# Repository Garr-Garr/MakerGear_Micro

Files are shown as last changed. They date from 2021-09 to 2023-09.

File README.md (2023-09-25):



# Introducing the MakerGear MICRO! 

### Description:

This 3D printed 3D printer is designed to be a fun, inexpensive, and easy to build open source project for anyone and everyone! With so many of our customers being in education, we set out to create the perfect tool for STEM education that not only encourages students to use their school's 3D printers, but also helps them better understand the mechanics and technology behind them. Not only do we want users to be able to make their own 3D printer, but we want them to be able to make these printers their own! 

Use any filament, any color, and due to its compact design, it can be printed on (nearly) ANY midsize desktop 3D printer! We have also included the STEP files so feel free to improve or modify this design for whatever parts you may already have on hand.

With the help and feedback of the 3D printing community, we hope to further increase this project's accessibility so that kids of any age or adults with little to no experience can enjoy making their own 3D printer. So please take a look around and maybe try the build for yourself, and if you're up to it, get your kids, or grandkids, or nieces & nephews involved. 3D Printing has been and ALWAYS will be a community. Together we can make the world a better place.

## Specs:
3D-Printable  |   Open-Source   |  DIY 3D-Printer  |  Marlin 2.0  |  TMC2209 Slient Stepper Drivers  |  TFT LCD Screen  |  Bowden Extruder  |  MK8 Hotend (rated up to 250°C)  |  89x89x100mm Build Volume  |  12Volt Power Supply

## User Guides:



### Built from MakerGear Kit:

* [Getting Started Guide](https://github.com/MakerGear/MakerGear_Micro/blob/main/Guides/Built_From_Kit/MICRO%20Getting%20Started%20Guide%20(kit).pdf)
* [Mechanical Assembly Guide](https://github.com/MakerGear/MakerGear_Micro/blob/main/Guides/Built_From_Kit/MICRO%20Mechanical%20Assembly%20Guide%20(kit).pdf)
* [Wiring Guide](https://github.com/MakerGear/MakerGear_Micro/blob/main/Guides/Built_From_Kit/MICRO%20Wiring%20Guide%20(kit).pdf)

### Built from scratch:

* [Getting Started Guide](https://github.com/MakerGear/MakerGear_Micro/blob/main/Guides/Built_From_Scratch/MICRO%20Getting%20Started%20Guide%20(scratch).pdf)
* [Mechanical Assembly Guide](https://github.com/MakerGear/MakerGear_Micro/blob/main/Guides/Built_From_Scratch/MICRO%20Mechanical%20Assembly%20Guide%20(scratch).pdf)
* [Wiring Guide](https://github.com/MakerGear/MakerGear_Micro/blob/main/Guides/Built_From_Scratch/MICRO%20Wiring%20Guide%20(scratch).pdf)

## Hardware:

* [Printed Parts](https://github.com/MakerGear/MakerGear_Micro/tree/main/Hardware)

## Printer Slicing Profiles:
* [Simplify3D](https://github.com/MakerGear/MakerGear_Micro/tree/main/Slicer_Profiles/Simplify3D)
* [PrusaSlicer](https://github.com/MakerGear/MakerGear_Micro/tree/main/Slicer_Profiles/PrusaSlicer)

## USB Driver:

While the Micro is fully controllable using the LCD screen and an SD Card/USB stick, you can directly connect the Micro to your computer via USB by downloading the USB drivers from BigTreeTech's page below:

> https://github.com/bigtreetech/BIGTREETECH-SKR-mini-E3/tree/master/firmware/mapleDrv-USBdriver

## Building Marlin 2.0 (Version: [2.0.9.1](https://github.com/MarlinFirmware/Marlin/releases/tag/2.0.9.1))
The firmware is already compiled and ready to upload onto your Micro, but you'd like to make any upgrades or changes to the firmware you'll need to compile the firmware. To compile and upload the firmware you'll need [Arduino IDE 1.8.8 or newer](https://www.arduino.cc/en/main/software) or [PlatformIO](http://docs.platformio.org/en/latest/ide.html#platformio-ide). Detailed build and install instructions are posted at:

  - [Installing Marlin (Arduino)](http://marlinfw.org/docs/basics/install_arduino.html)
  - [Installing Marlin (VSCode)](http://marlinfw.org/docs/basics/install_platformio_vscode.html).

## Inquiries:

Please contact "Print@MakerGear.com" if you have any questions, concerns, or even general feedback on the project!

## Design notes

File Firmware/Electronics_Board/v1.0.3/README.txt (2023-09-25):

Step 1: Format a MicroSD Card to the "FAT32" or "exFAT" filesystem

Step 2: Copy the "Firmware.bin" file onto the SD card

Step 3: Safely eject the SD card from your computer

Step 4: Insert the firmware SD card into the MicroSD card port on the SKR Mini e3 V2 electronics board

Step 5: Reset or reboot the printer (There is a small white reset button close to the MicroSD card adapter on the board)

Step 6: The TFT LCD screen should automatically connect once the firmware is finished uploading

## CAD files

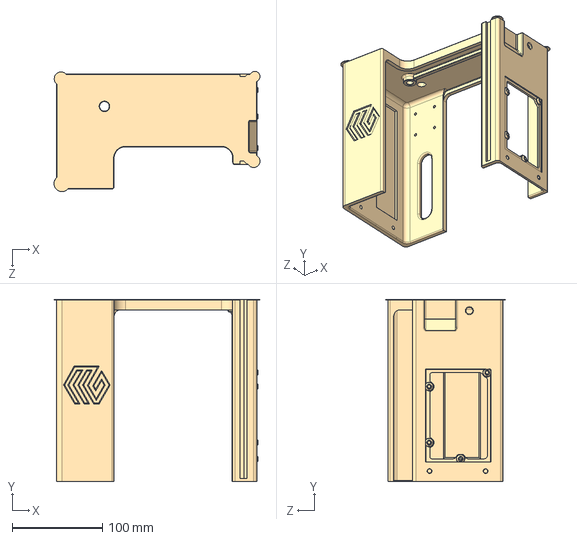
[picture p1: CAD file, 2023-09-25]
Hardware/STEP_Files/MICRO_Top.STEP
228.6 x 202.3 x 133.5 mm

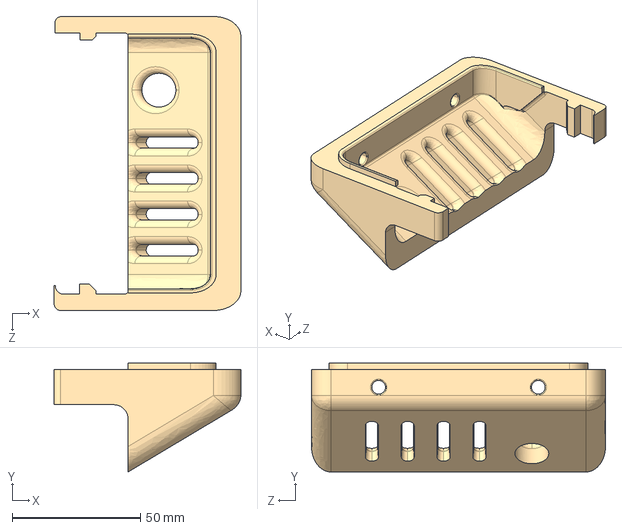
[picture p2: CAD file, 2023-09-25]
Hardware/STEP_Files/MICRO_ElectronicsCaseBase.STEP
72.7 x 42.5 x 114.6 mm

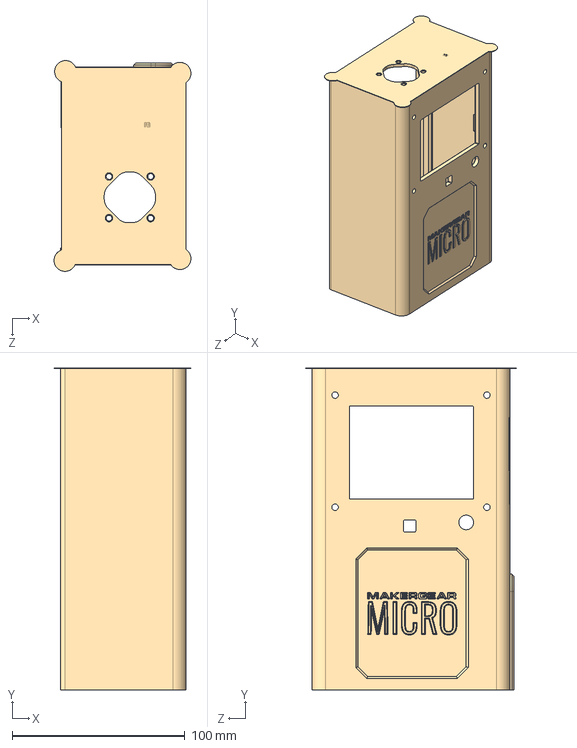
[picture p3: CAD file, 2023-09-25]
Hardware/STEP_Files/MICRO_ElectronicsCase.STEP
79.3 x 186.6 x 122.2 mm

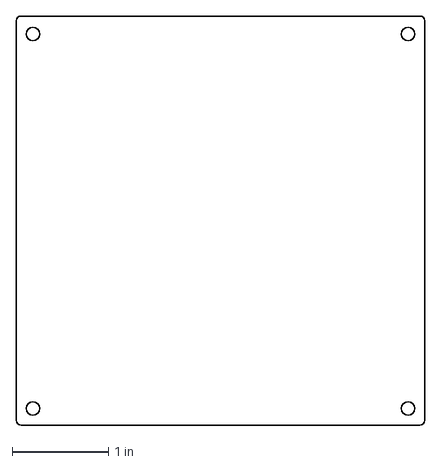
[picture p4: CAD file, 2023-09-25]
Hardware/STEP_Files/MICRO_LaserCutBed.DXF
4.25 x 4.26 in

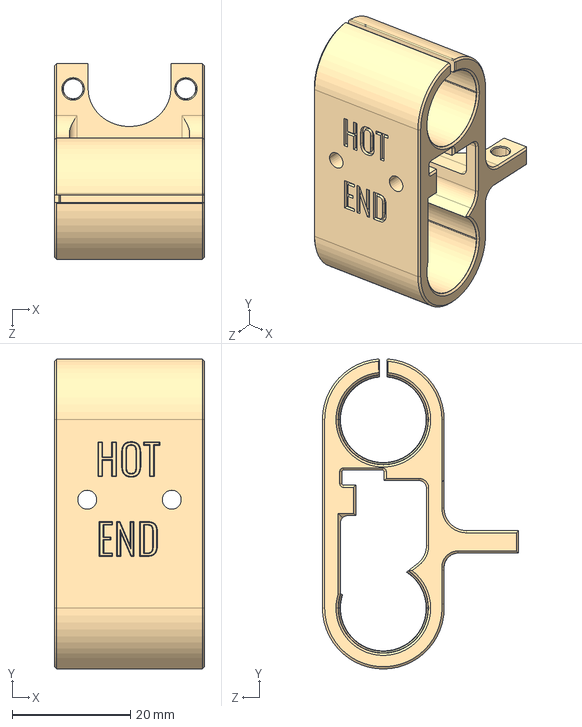
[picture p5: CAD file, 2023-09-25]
Hardware/STEP_Files/MICRO_HotEndMount.STEP
25.4 x 52.4 x 33.2 mm

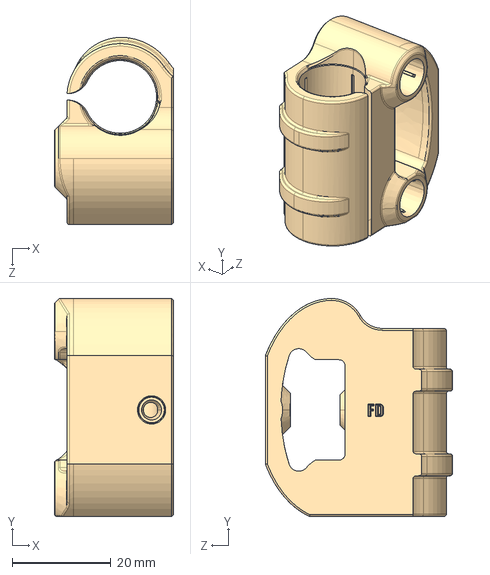
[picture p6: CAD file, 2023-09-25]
Hardware/STEP_Files/MICRO_XIdlerMount.STEP
24.1 x 44.1 x 37.9 mm

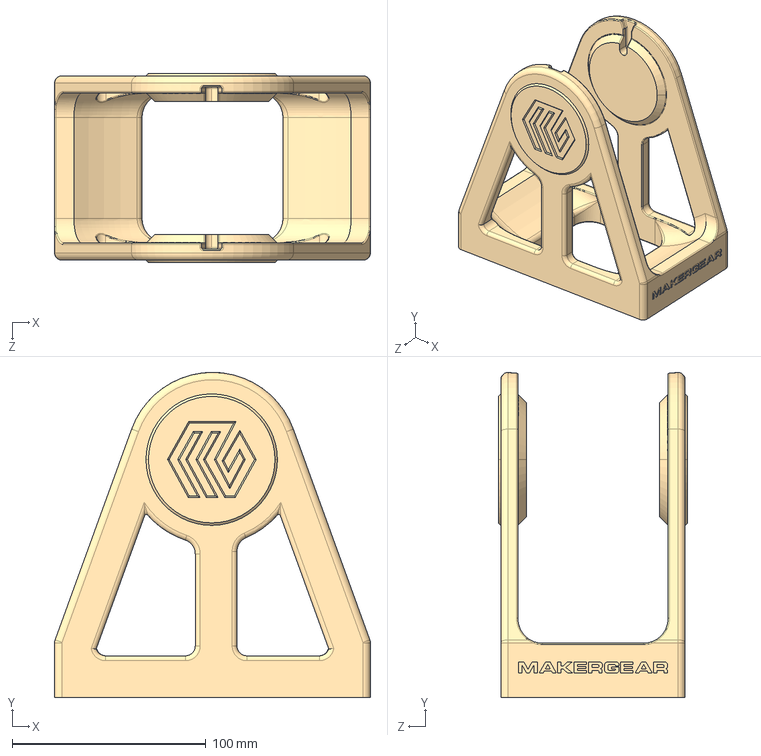
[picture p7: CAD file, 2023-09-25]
Hardware/STEP_Files/MICRO_SpoolHolder.STEP
163.2 x 168.0 x 97.8 mm

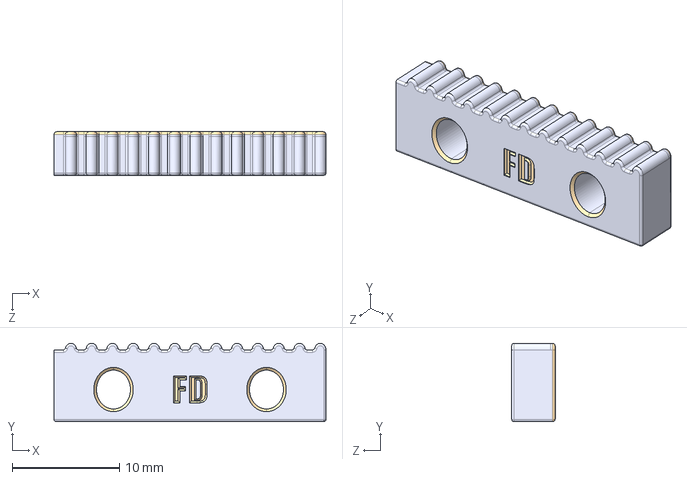
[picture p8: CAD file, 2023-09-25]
Hardware/STEP_Files/MICRO_XBeltGrip.STEP
25.4 x 7.32 x 4.06 mm

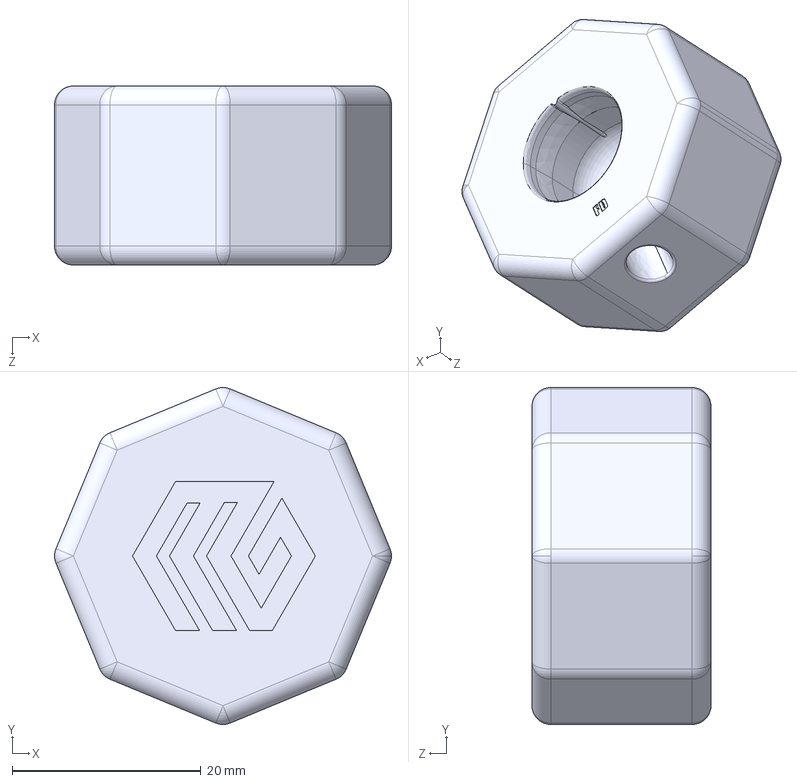
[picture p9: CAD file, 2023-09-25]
Hardware/STEP_Files/MICRO_ZKnob.STEP
35.8 x 35.8 x 19.0 mm

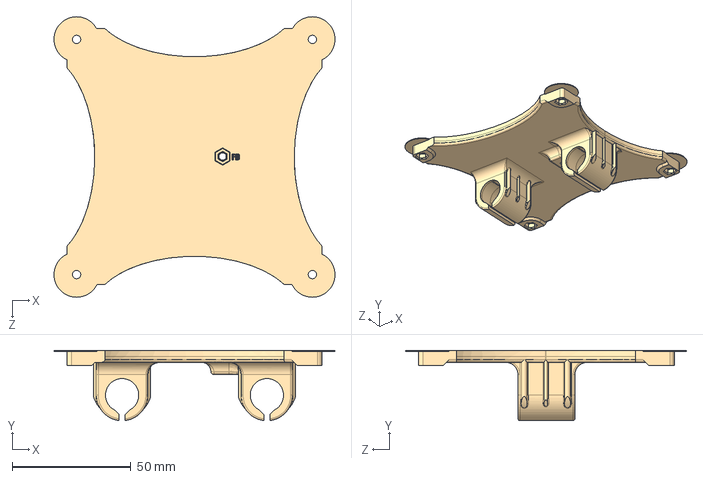
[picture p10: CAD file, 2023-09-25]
Hardware/STEP_Files/MICRO_Bed.STEP
118.3 x 29.6 x 118.1 mm

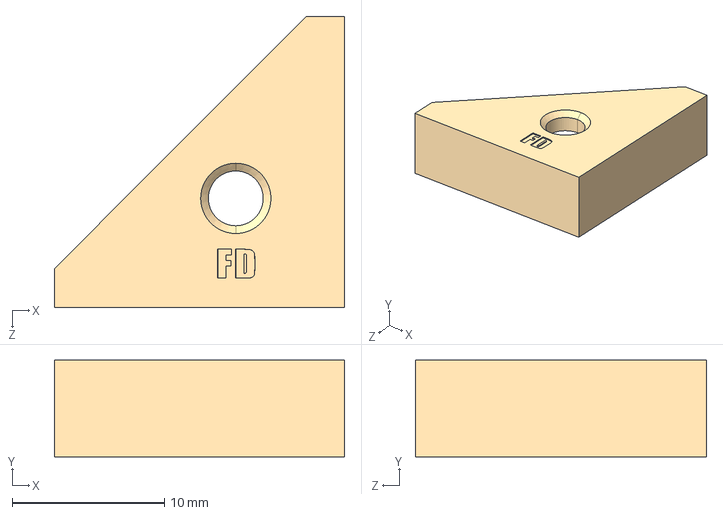
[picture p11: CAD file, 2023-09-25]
Hardware/STEP_Files/MICRO_BedClip.STEP
19.1 x 6.35 x 19.1 mm

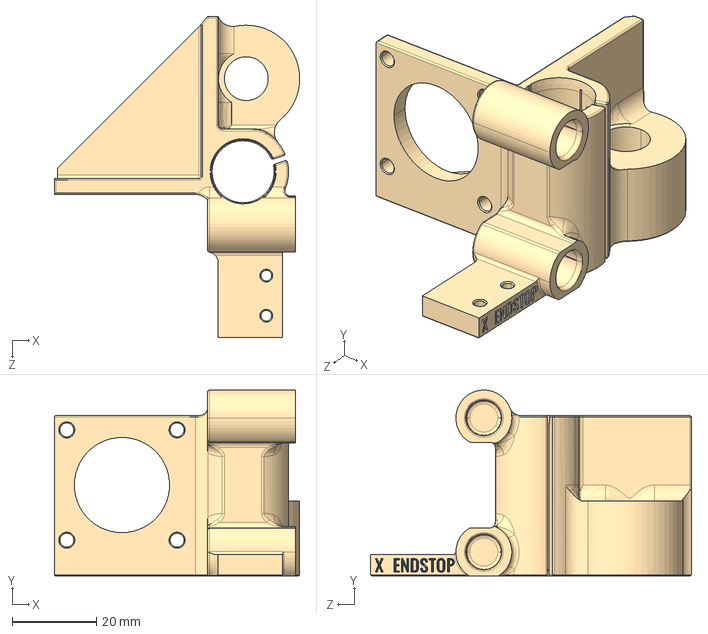
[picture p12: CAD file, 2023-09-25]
Hardware/STEP_Files/MICRO_XMotorMount.STEP
58.3 x 44.2 x 76.2 mm

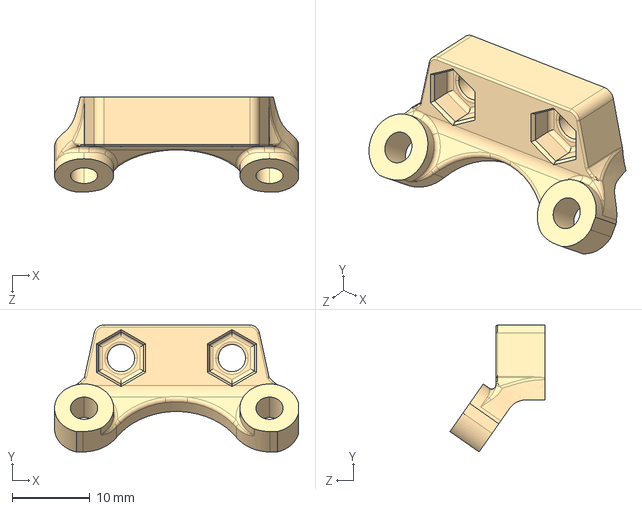
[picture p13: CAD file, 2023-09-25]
Hardware/STEP_Files/MICRO_FanMount.STEP
31.4 x 16.4 x 12.2 mm

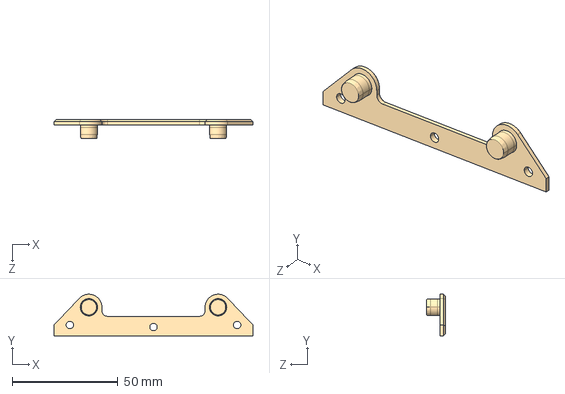
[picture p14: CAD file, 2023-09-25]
Hardware/STEP_Files/MICRO_YStop.STEP
93.9 x 19.6 x 9.02 mm

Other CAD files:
Hardware/STL_Files/MICRO_Bed.stl
Hardware/STL_Files/MICRO_BedClip.stl
Hardware/STL_Files/MICRO_ElectronicsCase.stl
Hardware/STL_Files/MICRO_ElectronicsCaseBase.stl
Hardware/STL_Files/MICRO_FanMount.stl
Hardware/STL_Files/MICRO_HotEndMount.stl
Hardware/STL_Files/MICRO_XIdlerMount.stl
Hardware/STL_Files/MICRO_XMotorMount.stl
Hardware/STL_Files/MICRO_YStop.stl
Hardware/STL_Files/MICRO_ZKnob.stl

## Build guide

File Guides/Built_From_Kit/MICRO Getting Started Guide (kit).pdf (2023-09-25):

# MAKERGEAR

# MICRO

# GETTING STARTED GUIDE

BUILT FROM KIT EDITION

# READ EVERYTHING PLEASE!

If you have chosen to build this thing from scratch, there are SO MANY little tiny things that might go wrong... So, we made one of our hyperactive engineers sit down & spend a COUNTLESS number of HOURS producing LOTS of detailed documentation to help YOU succeed. We’ll be honest there is like a LOT of verbiage in the next 10 pages & it might get boring, but you should read it. All of it. If not for yourself, do it for that poor engineer & the nights he worked late in

the hopes of making YOUR life easier.
Don’t let all that hard work be made in vain.

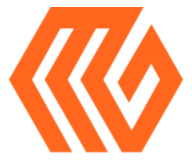
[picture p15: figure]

1

# BEFORE PLUGGING IN

## A Convenient Checklist to Make Sure Nothing Blows Up… Just Kidding

-Check EVERY wire connection! Each connector used in this kit should provide a nice snug connection either popping into place or being latched together. NO connection should be loose or easily removable. If a connection does seem loose, double check that it is plugged into the correct location with the proper orientation.
-Physically slide the machine’s X, Y, & Z axis to confirm a proper mechanical assembly.
-Start with the Y axis by sliding the bed back & forth. Ensure that it travels smoothly without much resistance and can reach the Y End Stop successfully. The Y End Stop should click once the bed reaches it. When sliding the bed make sure the belt properly rotates both the Idler Pulley at the front of the machine, as well as the Drive Pulley mounted onto the Y Motor.
-Now check the X Axis by sliding the Hot End Mount from side to side. Confirm that it slides smoothly without interruption & that it successfully triggers the X End Stop once slid all the way to the left. Give the Hot End assembly a very light wiggle to check that it is securely fastened to the Hot End Mount. Lastly check that the belt is held snug withing the Hot End Mount by giving it a few gently tugs. This belt MUST be secure for your machine to succeed.
-Lastly check the Z Axis by turning the Z Knob both clockwise and counterclockwise. The entire X Axis assembly should move up and down relatively easy. You will feel the motor subtly click repeatedly as you manually rotate the Z Knob, this is normal. Make sure to not dig the tip of the nozzle into the bed when lowering or grind the entire assembly into the roof when raising the axis. -Make sure to raise the Hot End at least an inch above the bed before plugging in your machine. The BL Touch Probe will deploy every time the machine is turned on and needs space to fully deploy or else it will fail its initial start up tests & the machine will need restarted.

2

# NOW PLUG IN!

## We are ALMOST there… Just a Little Housekeeping First

-As mentioned on the last page, once plugged in the BL Touch probe will initiate a short test in which it deploys & retracts twice each. If it does not do this, something could be wrong with the probe or its connection.
-Once the screen turns on, you might be greeted by the prompt below, in which case you’ll select “Touch Mode”

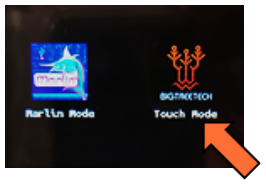
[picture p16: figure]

-Does “Marlin Mode” work with this device? Yes. Is it nearly as cool? NO… but if you insist or if you accidentally hit the wrong mode, pressing the screen’s knob like a button, and holding it for several seconds will allow you to return to this selection screen.
-You should end up at a screen like the one pictured below. You will also be greeted by a “Bed Leveling Failed” prompt. Ignore it. We’ll address that a few steps from now. Make sure to follow along with the orange arrows provided by this guide.

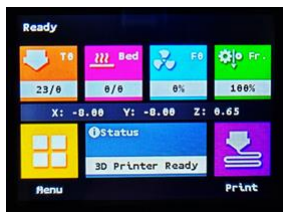
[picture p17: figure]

3

# AFTER PLUGGING IN

## These Next Steps MUST be Completed Before Your MICRO’s First Print

Next, we want to test the 3 axis motors by homing all 3 axis. Both the X and Y axis will move into their respective limit switches, activating them twice before settling into their home position. The Z axis will raise slightly and then lower the probe into the center of the bed twice. If all 3 axis home as described, proceed to the next step. If not, there could be an issue with your motor connections.

## HOW TO HOME YOUR MACHINE

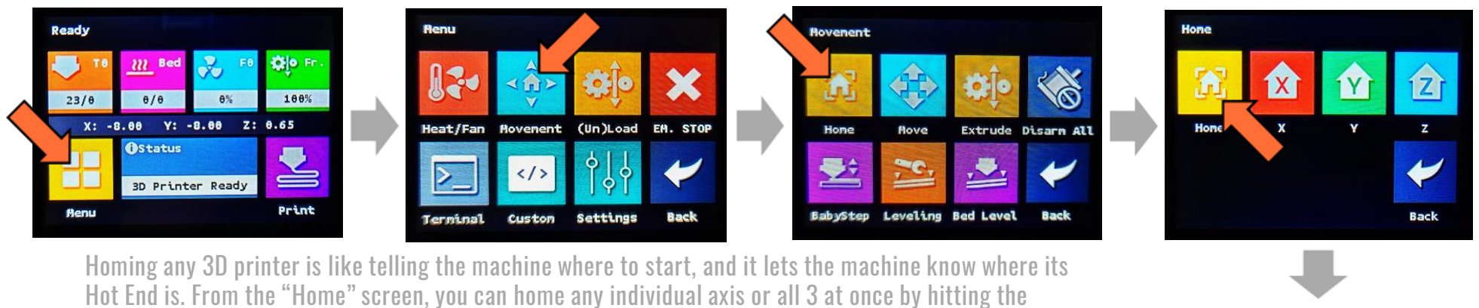
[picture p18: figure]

Homing any 3D printer is like telling the machine where to start, and it lets the machine know where its Hot End is. From the “Home” screen, you can home any individual axis or all 3 at once by hitting the yellow “Home” button. Always make sure the bed is clear & nothing can impede the machine’s movement before homing. Let the homing sequence finish completely before advancing to the next steps.

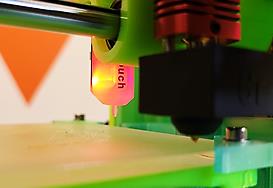
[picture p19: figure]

4

# AFTER PLUGGING IN [cont.]

Once homing is completed, the probe offset must be set. This tells the MICRO how far the tip of the nozzle is from the tip of the BL Touch probe. If set correctly your first layers will be placed the perfect distance above the bed and will properly adhere to the bed surface. If this value is too high, the nozzle will be too far from the bed & none of the printed plastic will stick properly to the bed. If too low, the nozzle will be ground into the bed and the plastic will come out too squished or not at all.

## SETTING THE PROBE OFFSET

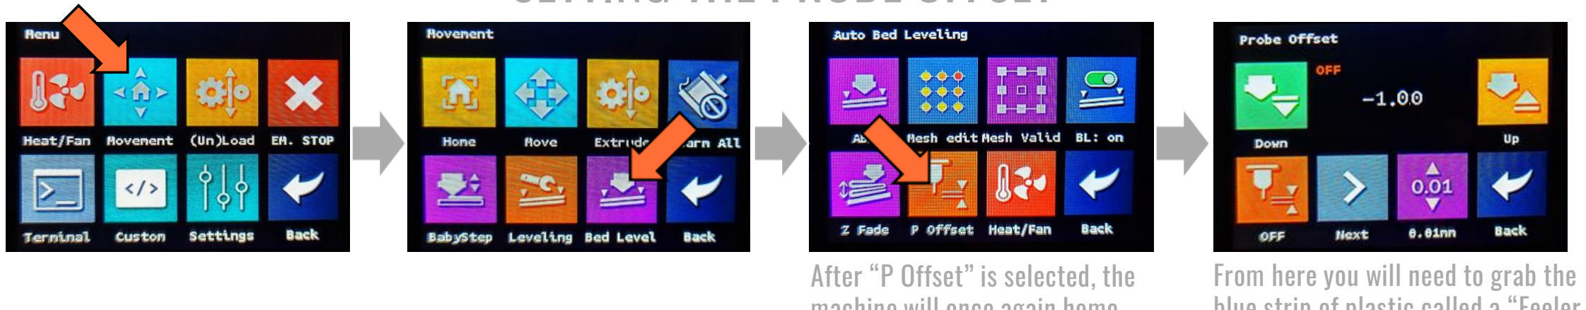
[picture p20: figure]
After “P Offset” is selected, the; From here you will need to grab the

machine will once again home the Z axis.

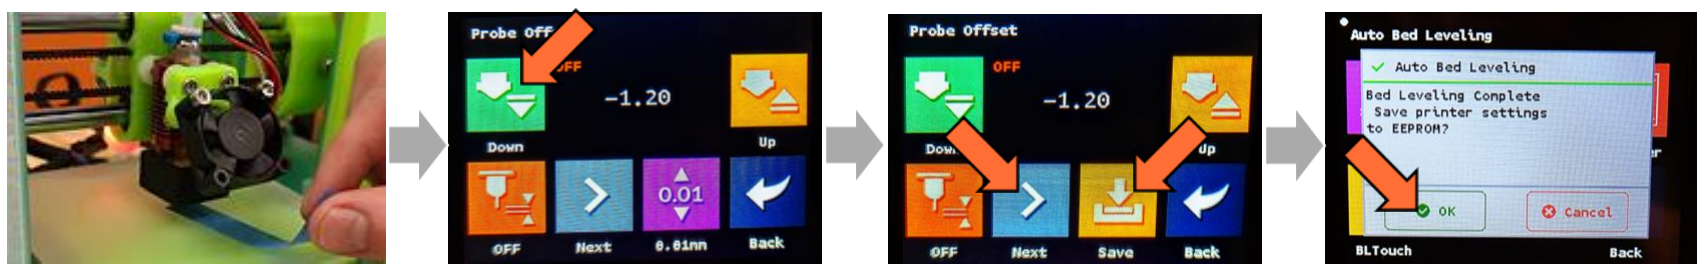
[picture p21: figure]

Place the Feeler Gauge beneath the tip of the nozzle and use the “Down” button to lower the nozzle towards the bed. Lower the nozzle until it just barely touches the Feeler Gauge. The increments in which the nozzle moves can be tweaked via the purple button initially labeled, “0.01mm”

Once you feel that the perfect offset value has been reached, hit the “Next” button twice or until the “Save” button appears next to hit. Select “Save” and the following prompt will pop up to which you respond, “OK” blue strip of plastic called a “Feeler Gauge” from the provided tool kit.

5

This setting is essentially the equivalent of Automatic Bed Leveling which will make sure that your first layers are always flat & flush with your bed. If not set properly, the nozzle will vary in its distance from the bed while printing. This can cause portions of the print to not stick properly or not extrude at all which will almost always cause your print to fail

## ACTIVATING BED LEVEL COMPENSATION

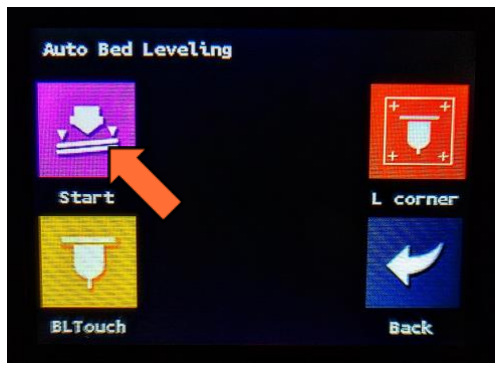
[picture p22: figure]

Pressing “Start” will lead into the machine’s probing sequence during which the printer will generate a mesh. This mesh basically let’s the printer know how the bed is shaped/slanted & will use the Z Motor to compensate for these variations while printing.

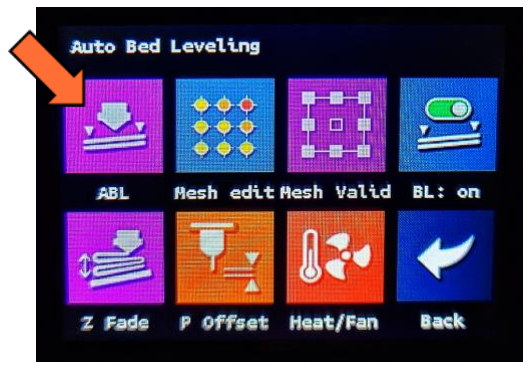
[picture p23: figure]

Return once more to the “Auto Bed Leveling” screen (found under the “Movement” option in the main menu)

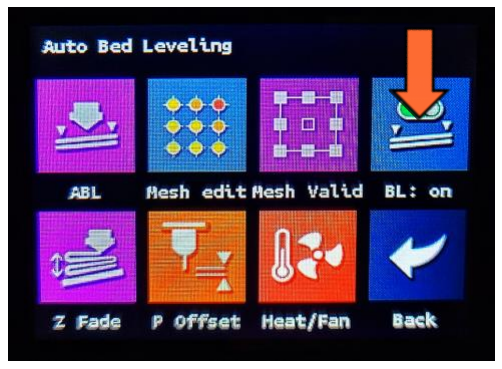
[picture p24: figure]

Before returning to the main menu, make sure the BL Touch is activated by hitting this button. It should display “BL: on” and can be toggled on & off with each press.

# AFTER PLUGGING IN [cont.]

6

Finally, we will be loading filament into your MICRO. Only use a PLA that has a recommended printing temperature range that includes 190°C or below. You may need to straighten out the first couple inches of the filament’s end to help thread it into the filament drive.

## LOADING THE FILAMENT

# AFTER PLUGGING IN [cont.]

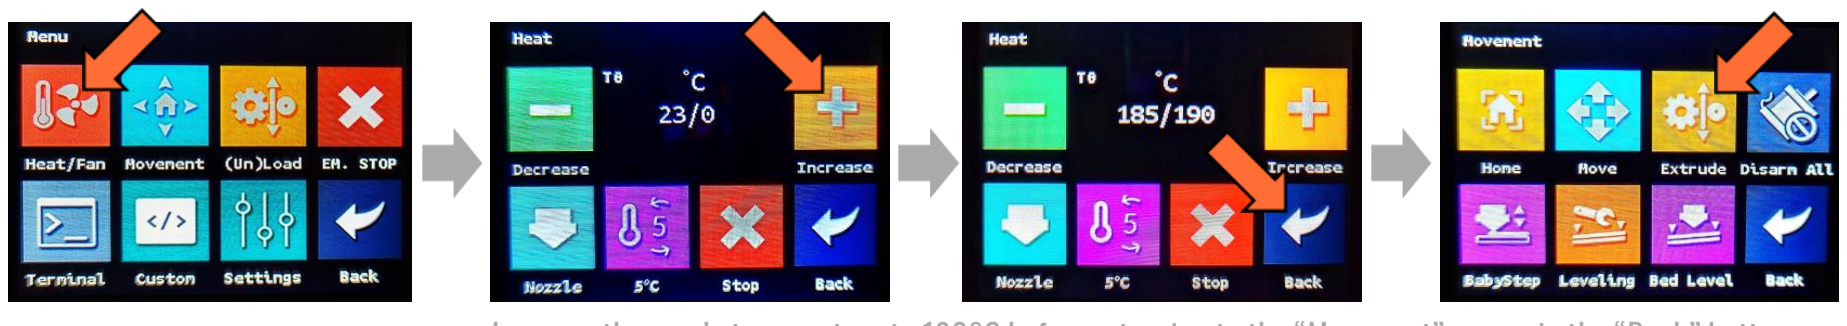
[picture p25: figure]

Increase the nozzle temperature to 190°C before returning to the “Movement” menu via the “Back” button. The left temperature value in white is the actual temp, while the right value is the temp you set it to.
You can adjust your temperature increments via the purple button initially labeled “5°C”

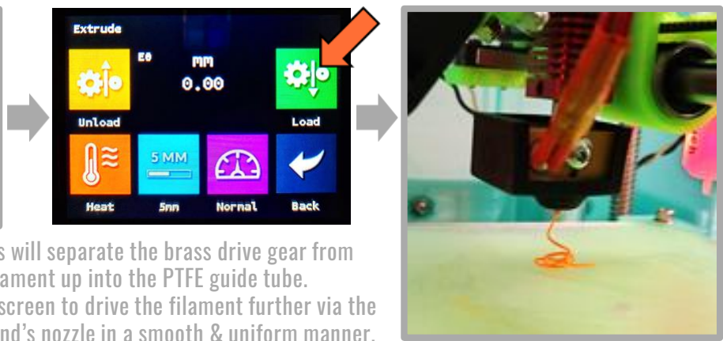
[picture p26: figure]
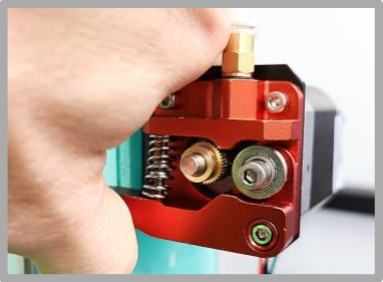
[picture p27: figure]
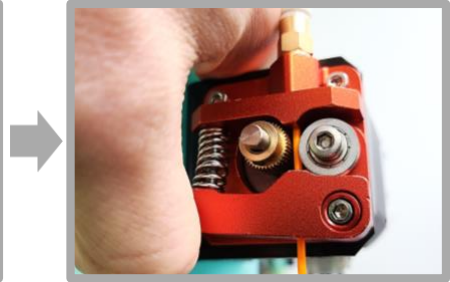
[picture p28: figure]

Pinch the lever of the MICRO’s filament drive to compress the spring. This will separate the brass drive gear from the silver bearing/pulley creating a space for you to feed an end of the filament up into the PTFE guide tube. Manually feed the filament until it reaches the hot end, and then use the screen to drive the filament further via the “Load” button. Continue to load filament until it extrudes out of the hot end’s nozzle in a smooth & uniform manner.

7

# STARTING YOUR FIRST PRINT

## Wow… Here We Go!

-Make sure one more time that the print bed is clear and free of debris.
-Confirm that your filament is loaded, and that the spool is placed within a spool holder directly next to the filament drive. This spool of filament must be fed directly upwards into the filament drive allowing the filament to unwind in a natural manner. -Plug the included SD Card into the SD slot next to the touch screen. This is where you’ll store gcodes for all of your prints. -Confirm your MICRO is placed on a sturdy surface in a well-ventilated space.
-Start your print…

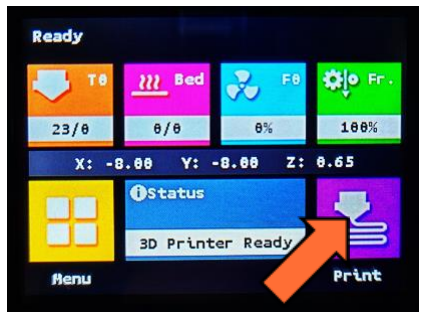
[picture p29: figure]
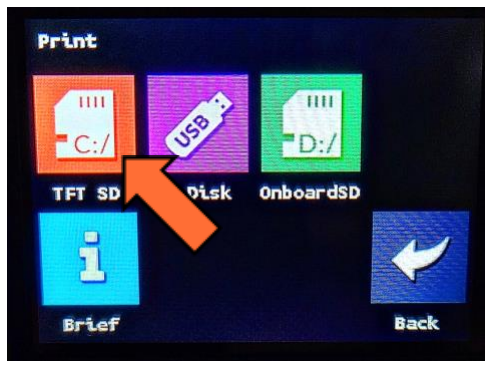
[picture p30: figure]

-Once heated up, the machine will go directly into its first layers. Be prepared to cancel the print if the first layers are not adhering properly. If the nozzle simply seems slightly too close or too far, you can use the Z Knob to make small adjustments, one click at a time.

Select the gcode file you’d like to print. We suggest starting with the “MICROVase” as a test.

8

# PRINTING WITH THE MICRO

## A Random List of Tips & Tricks to Set You up for Success

-ONLY use PLA when printing. You made a 3D printed 3D printer NOT an industrial machine for prototyping with exotic materials.
-We suggest printing on this machine with a layer height of .2mm or higher.
-A print speed of 40mm per second or slower is highly recommended. This will decrease the likelihood of the belts slipping or the smaller X and Y motors from skipping. These problems can be recognized by layer shifts mid print.
-NEVER Exceed a printing temperature of 200°C. Since we are using such a small cooling fan, over time the heat might leak upwards and start melting your printer if the nozzle temp is set too high.
-For the same reason as the previous point, NEVER operate the printer if the Hot End’s cooling fan is malfunctioning. Make sure this fan is running at the start of EVERY print. The fan should come on automatically anytime the nozzle temperature exceeds 30°C
-DO NOT remove the PTFE tubing or Nozzle from the Hot End Assemble unless absolutely necessary. With this style of Hot End, removing/replacing either one of these will highly increase your chances of the assembly clogging or getting jammed.
-NEVER operate your printer without the included blue collar fit snug onto the Hot End Assembly. This ensures the PTFE tube stays in place & reduces the risk of filament clogs
-Unload the filament when your machine is not in use. Leaving filament loaded in the printer when it is not in use increases the likelihood of your printer’s nozzle getting clogged.
-Unplug the MICRO when it is not printing for extended periods of time. You MUST let the nozzle completely cool below 30°C before turning the unit off.
-Have fun creating new things with a machine YOU created!

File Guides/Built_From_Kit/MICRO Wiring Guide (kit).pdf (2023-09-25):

# MAKERGEAR

# MICRO

# WIRING GUIDE

### BUILT FROM KIT EDITION

1

# WIRING TIPS & WARNINGS

-Included with the MakerGear MICRO kit, will be 3 separate wiring harnesses labeled “A”, “B”, & “C”
The harness used on each step will be designated on the bottom left-hand corner of the page.
-This guide primarily focuses on the connections into the SKR Mini Control Board. After plugging in each harness, make sure to plug the opposite ends into their respective connectors/components that are called out via the shrink wrap. Every connector is labeled directly on the wire, which port/connector/component it plugs into & the connections were designed to only fit in a single orientation. Be weary not to force any connectors to fit together that might not belong together.
-Due to minor variations in makes/models of the electronics, the proper orientation of some of the board’s ports may vary from the way they are pictured in this guide. Make sure to plug them in correctly as designated by their keying. DO NOT FORCE THEM INTO PLACE THE INCORRECT DIRECTION.

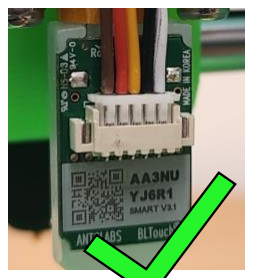
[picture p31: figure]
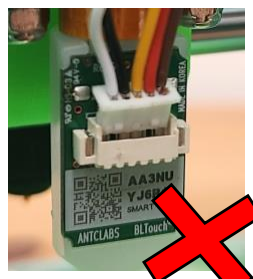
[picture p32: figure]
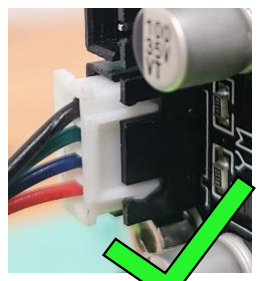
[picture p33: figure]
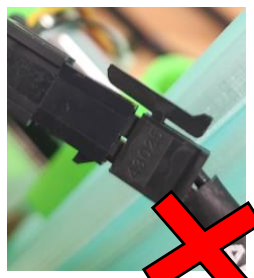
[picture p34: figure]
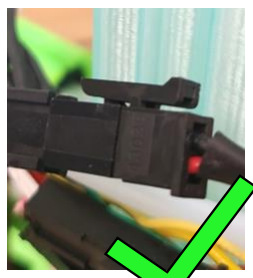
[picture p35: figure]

-Never remove connections by pulling solely on the wires. Grasp/pinch them via their plastic connectors
-Within some kits the coloring of the wires may vary slightly from that shown in this guide.
-Be cautious when handling the motherboard, not to accidentally connect/short any of the pins.

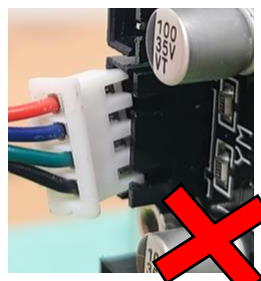
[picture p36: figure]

-Do NOT plug in or power up your machine until ALL connections are made. Once plugged in & powered up, do NOT connect or disconnect any pins or connectors & do not touch or adjust any of the screw terminals. Always disconnect power when making adjustments to the harnesses or their connectors.

2

# MOTHERBOARD OVERVIEW

## WHICH PORTS YOU WILL USE & WHAT THEY ARE FOR

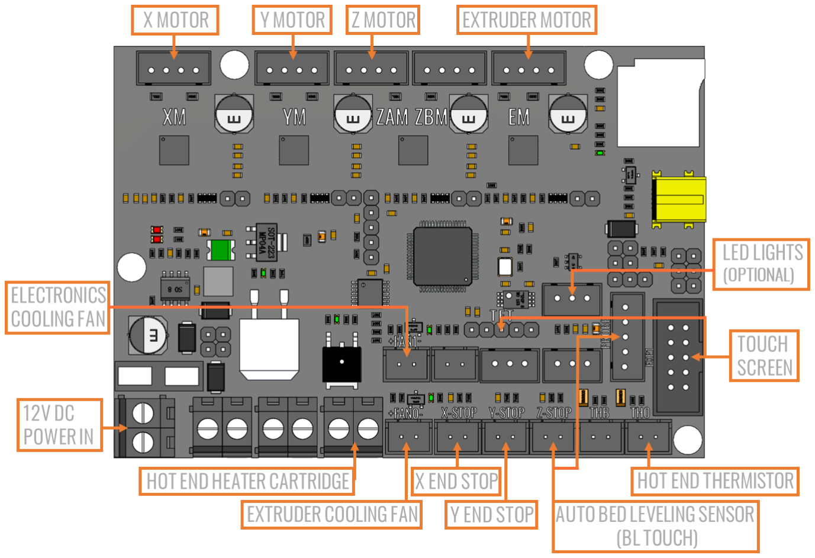
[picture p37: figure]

3

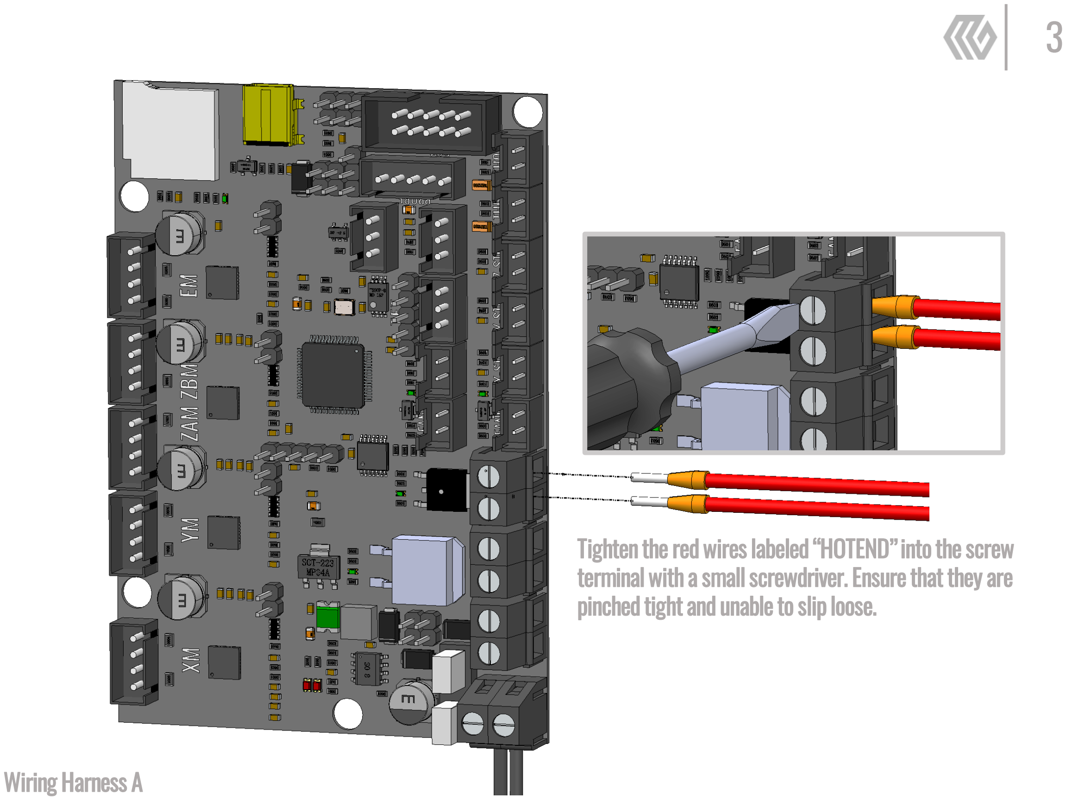
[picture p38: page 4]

## Tighten the red wires labeled “HOTEND” into the screw

## terminal with a small screwdriver. Ensure that they are

pinched tight and unable to slip loose.

## Wiring Harness A

4

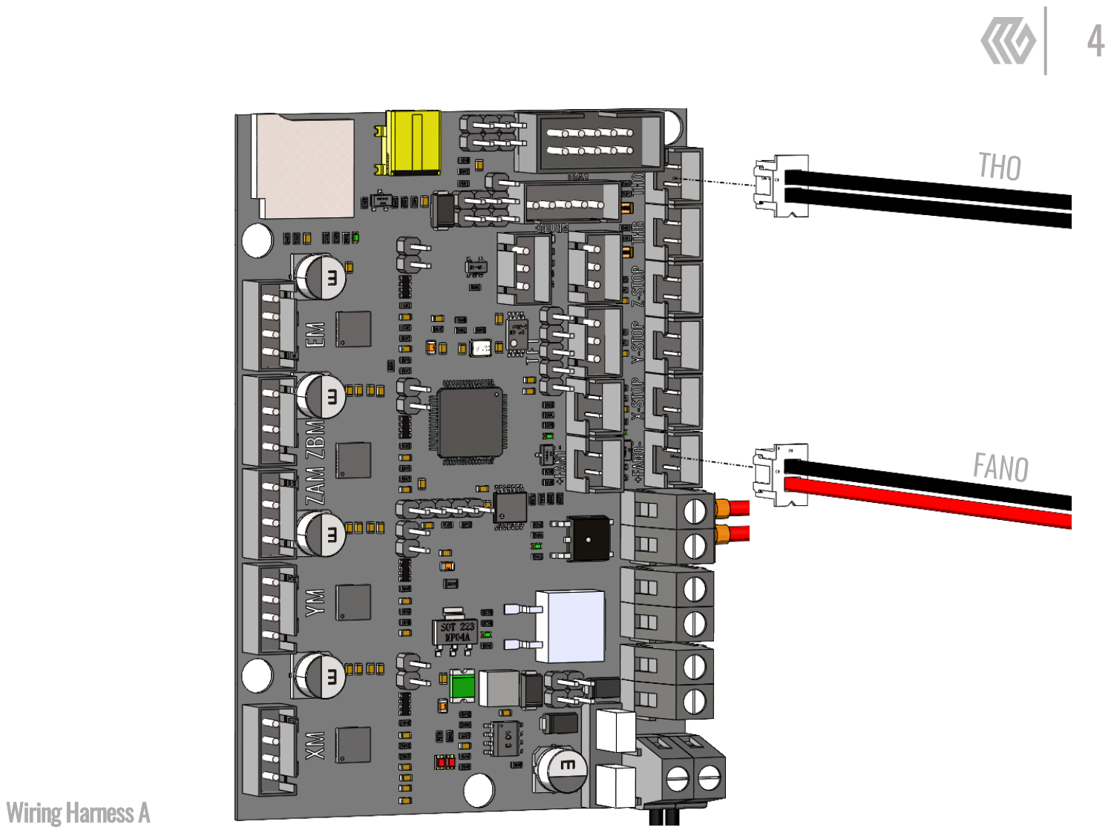
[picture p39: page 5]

## Wiring Harness A

5

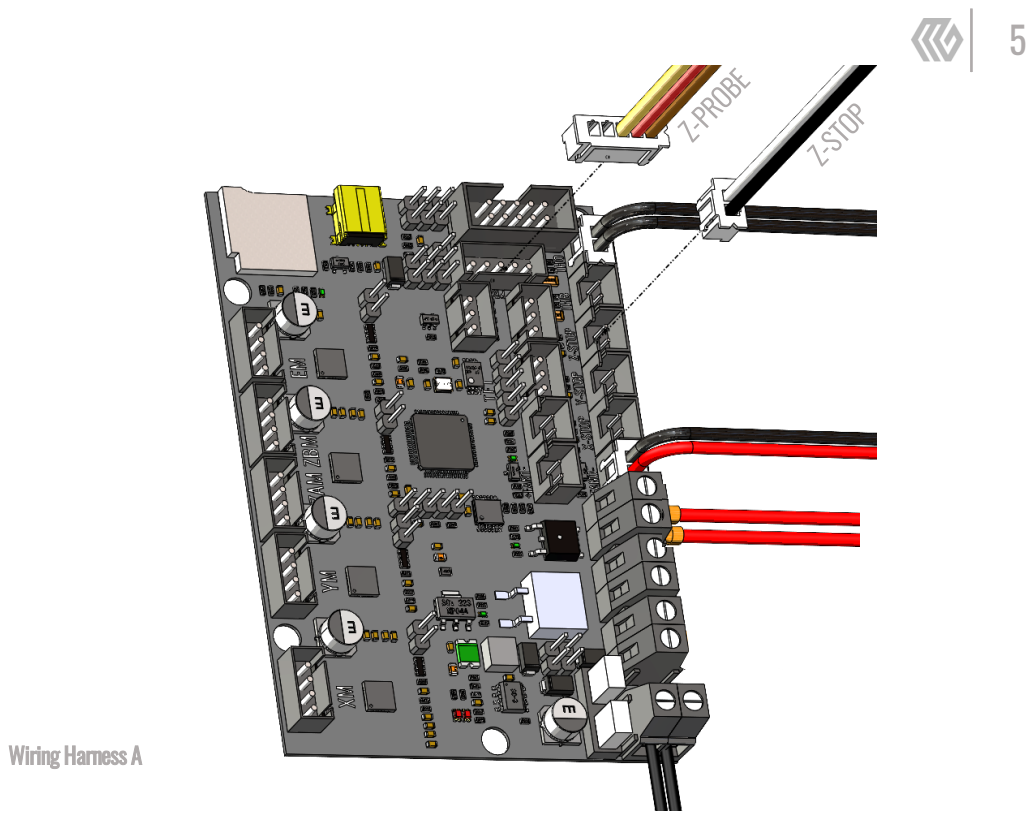
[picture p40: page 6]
Wiring Harness A

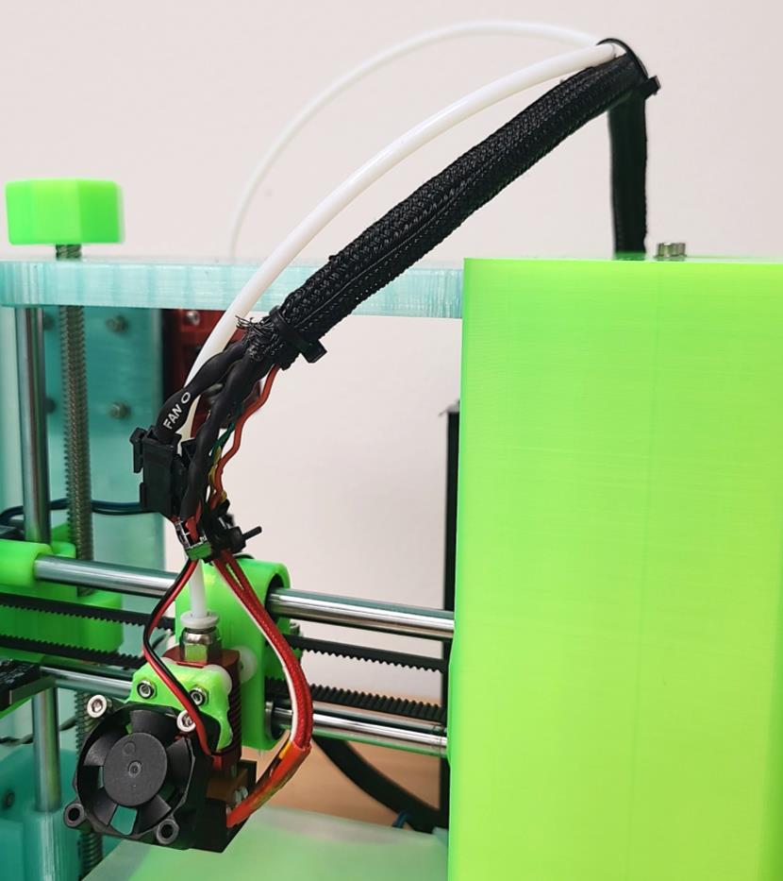
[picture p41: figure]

## The opposite end of Harness A must run OVER THE TOP of the MICRO. Once all connected, use several small zip ties to help manage the wires & bind the harness to the PTFE tubing. This will limit the harness from scraping the

top of the machine & keep it out of the tool head’s way.

6

7

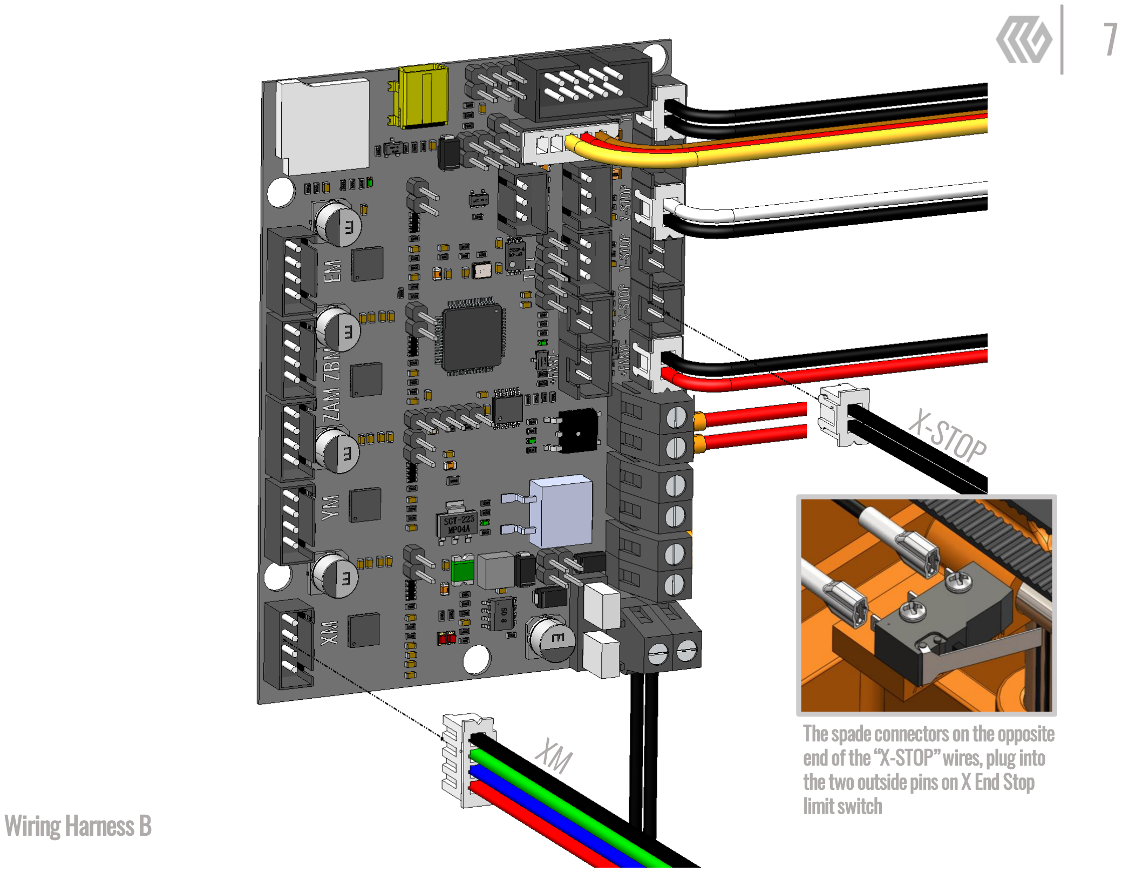
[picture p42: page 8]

The spade connectors on the opposite end of the “X-STOP” wires, plug into the two outside pins on X End Stop limit switch

## Wiring Harness B

8

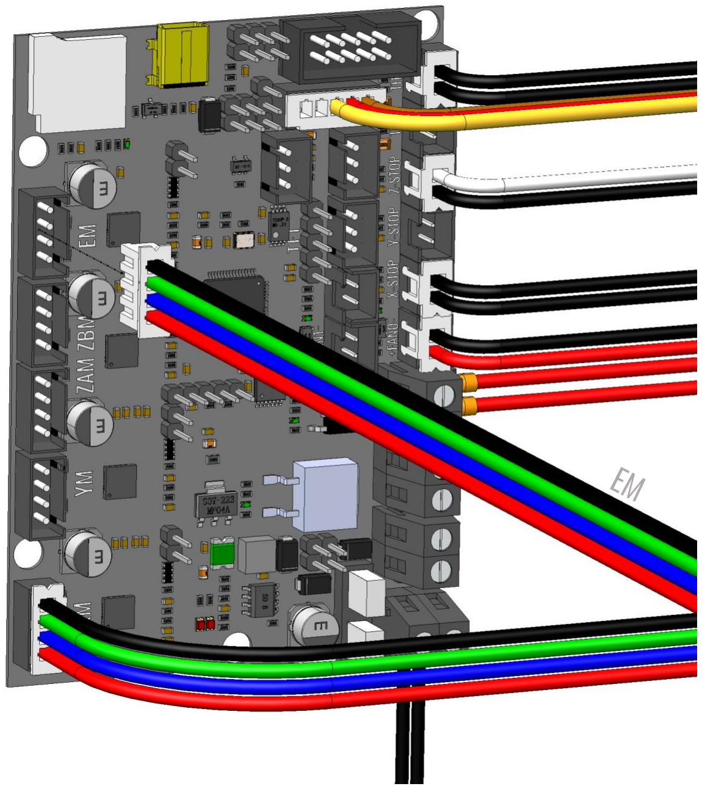
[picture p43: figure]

## Wiring Harness B

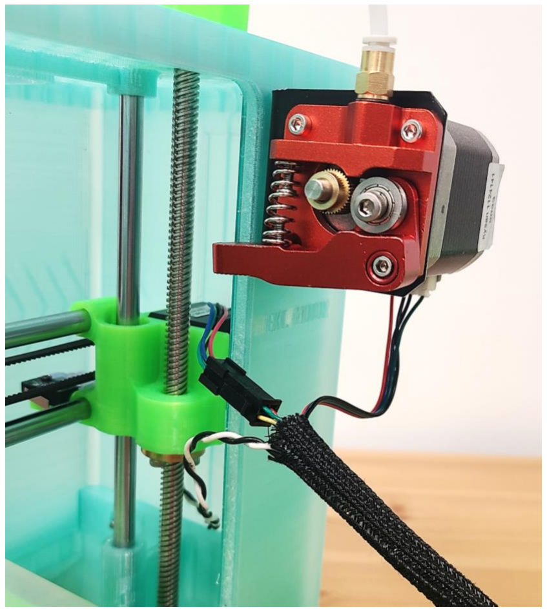
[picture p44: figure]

## The opposite end of Harness B will run behind the machine to connect to the X axis & Extruder Motor. Make sure to run the X Stop wires BEHIND the Z Motor & Z Linear Motion Rod. The updated Top design includes a cut away slot for

## both the X Motor & X Stop wires to run through to help

distance these from the moving parts of the machine.

9

10

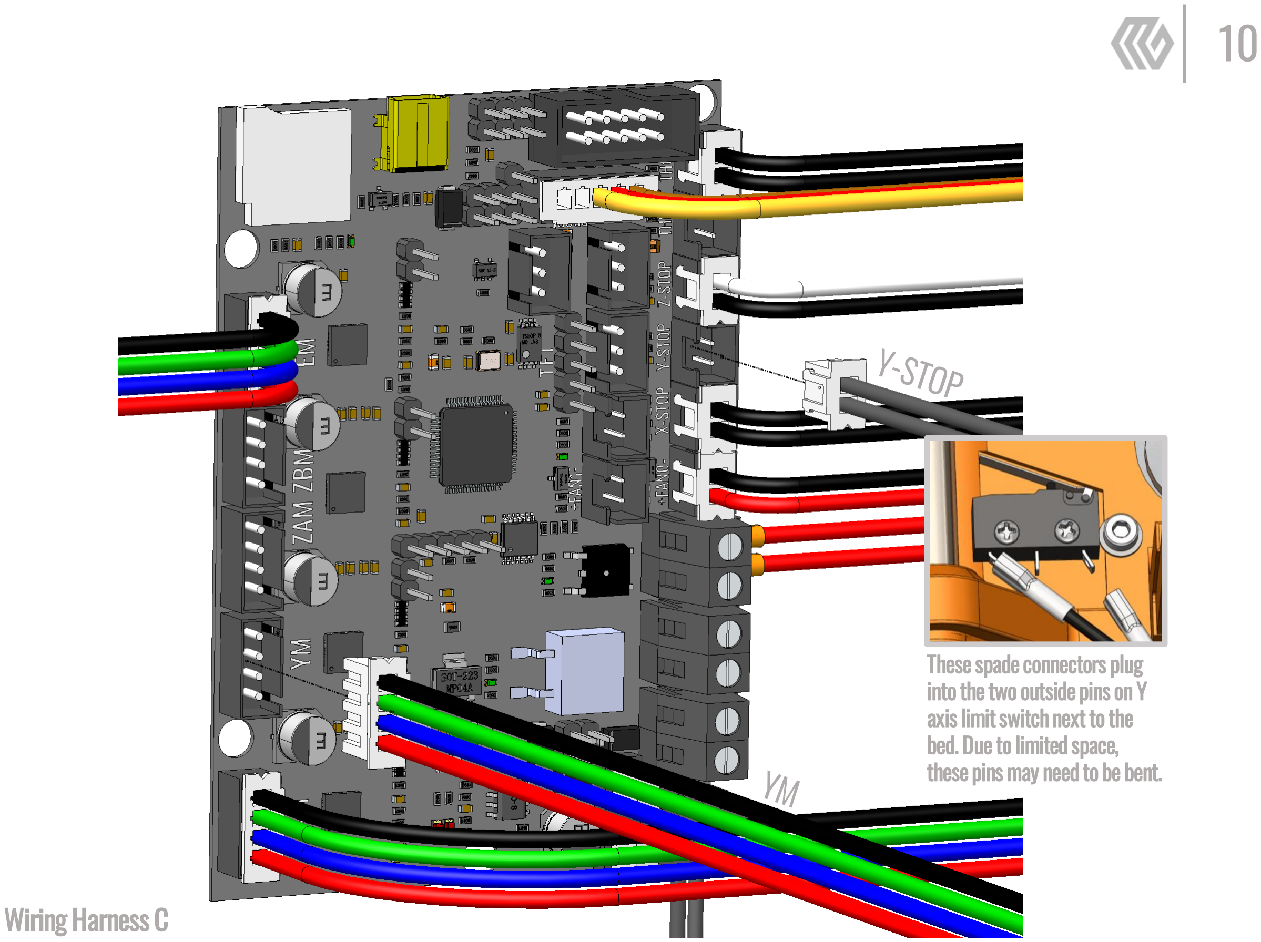
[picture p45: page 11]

## Wiring Harness C

These spade connectors plug into the two outside pins on Y axis limit switch next to the bed. Due to limited space, these pins may need to be bent.

11

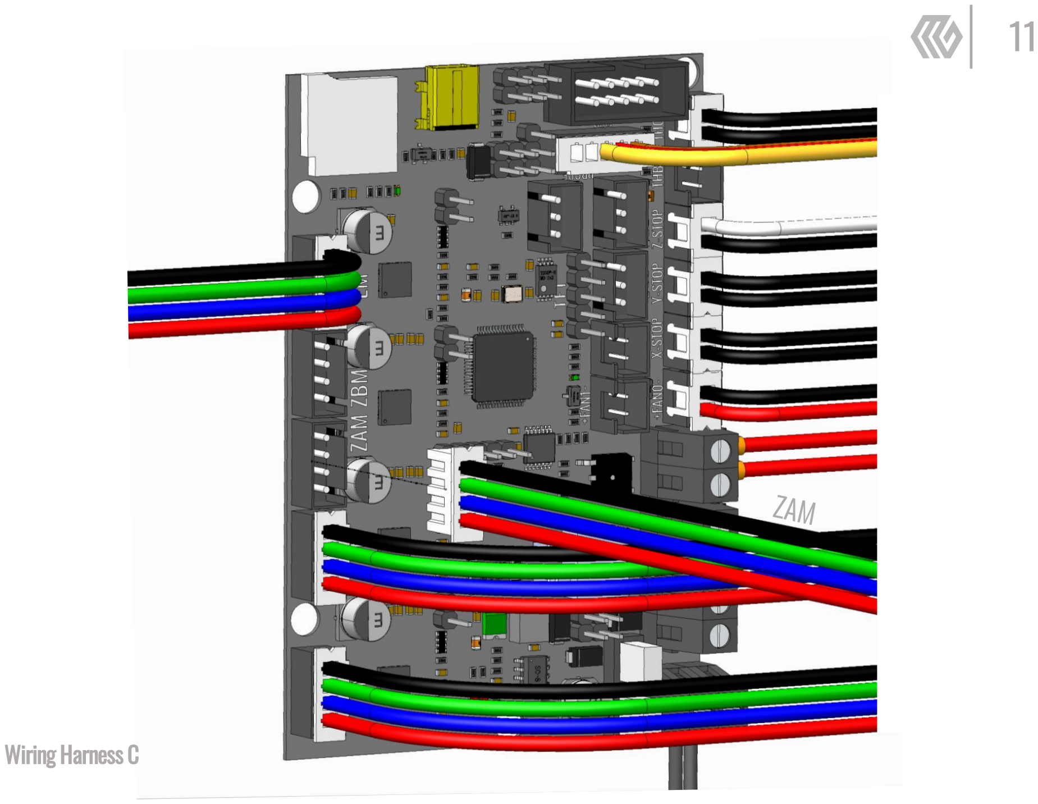
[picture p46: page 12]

## Wiring Harness C

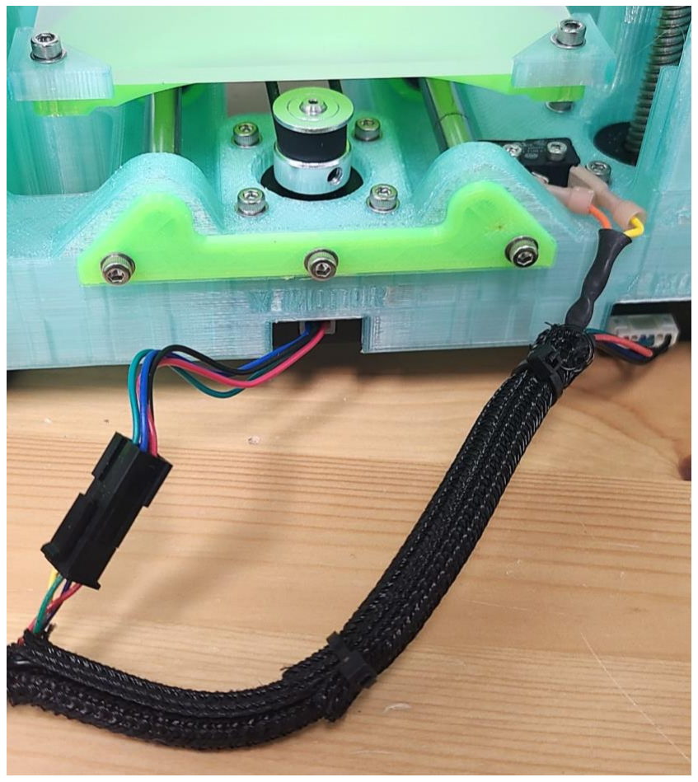
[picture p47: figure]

## The opposite end of Harness C simply runs behind the machine with all 3 parts connecting to the base. Make sure no portions of this harness are in the way of the bed’s linear

path in the Y direction.

12

13

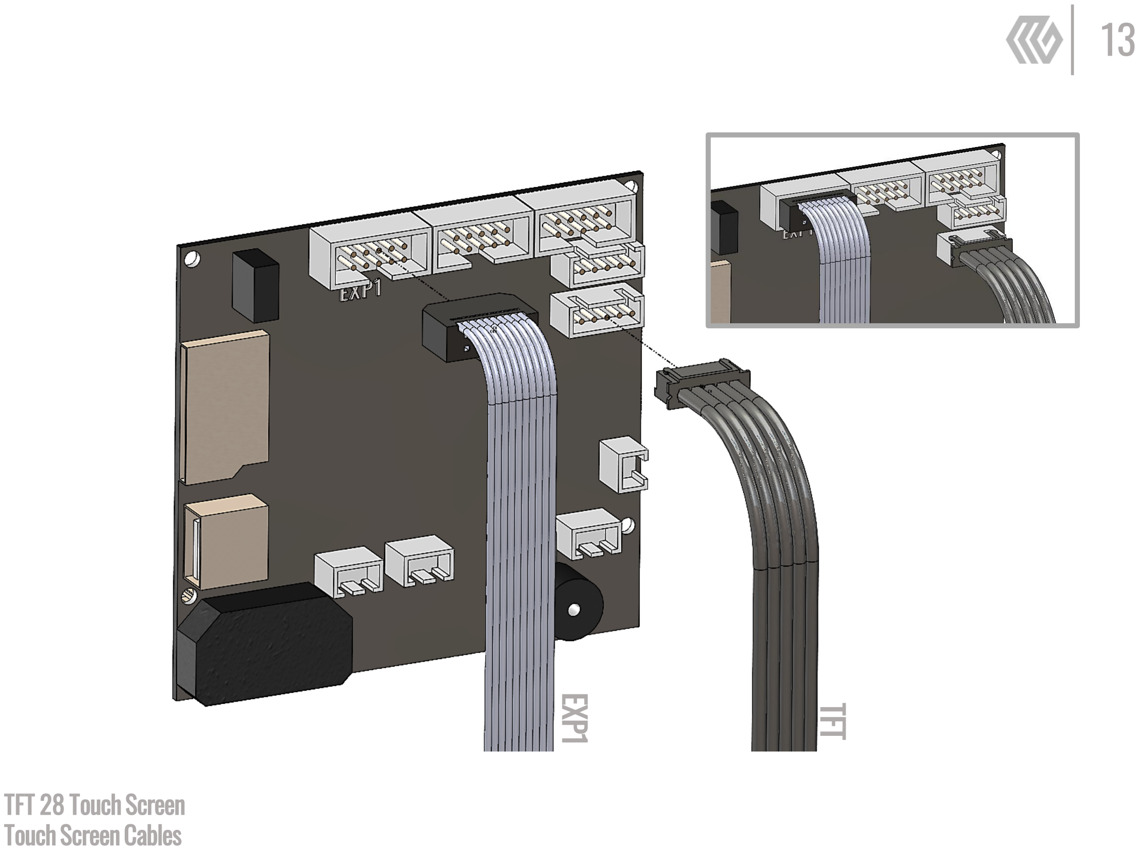
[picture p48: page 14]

## TFT 28 Touch Screen Touch Screen Cables

EXP1
TFT

14

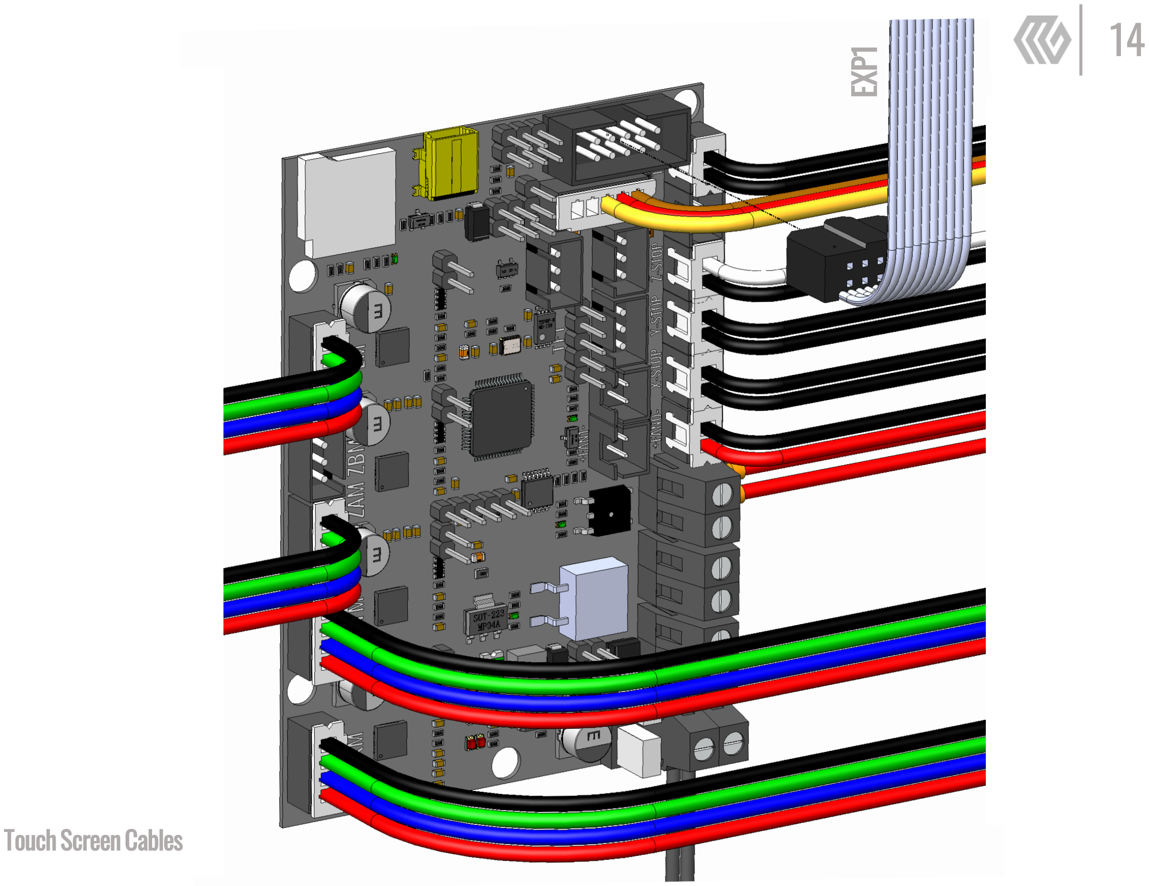
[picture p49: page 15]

EXP1

## Touch Screen Cables

15

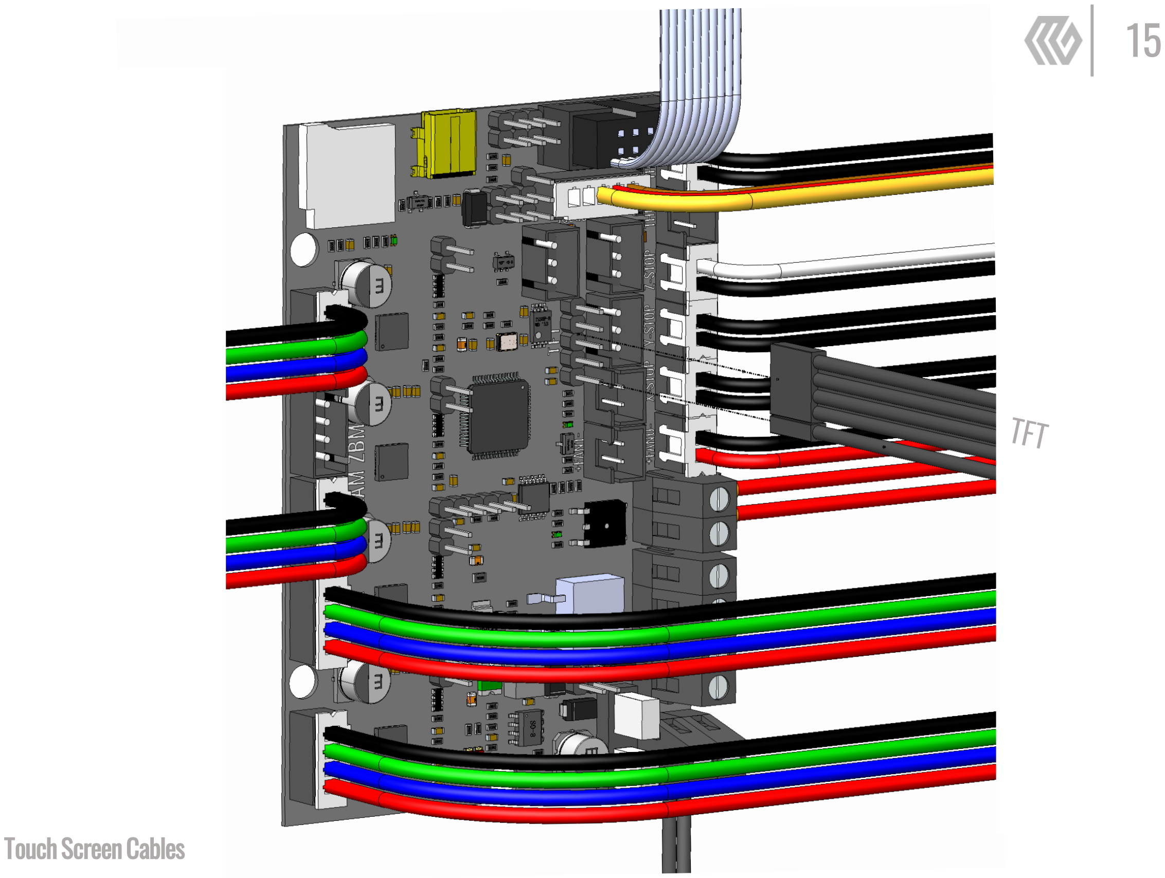
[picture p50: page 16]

## Touch Screen Cables

16

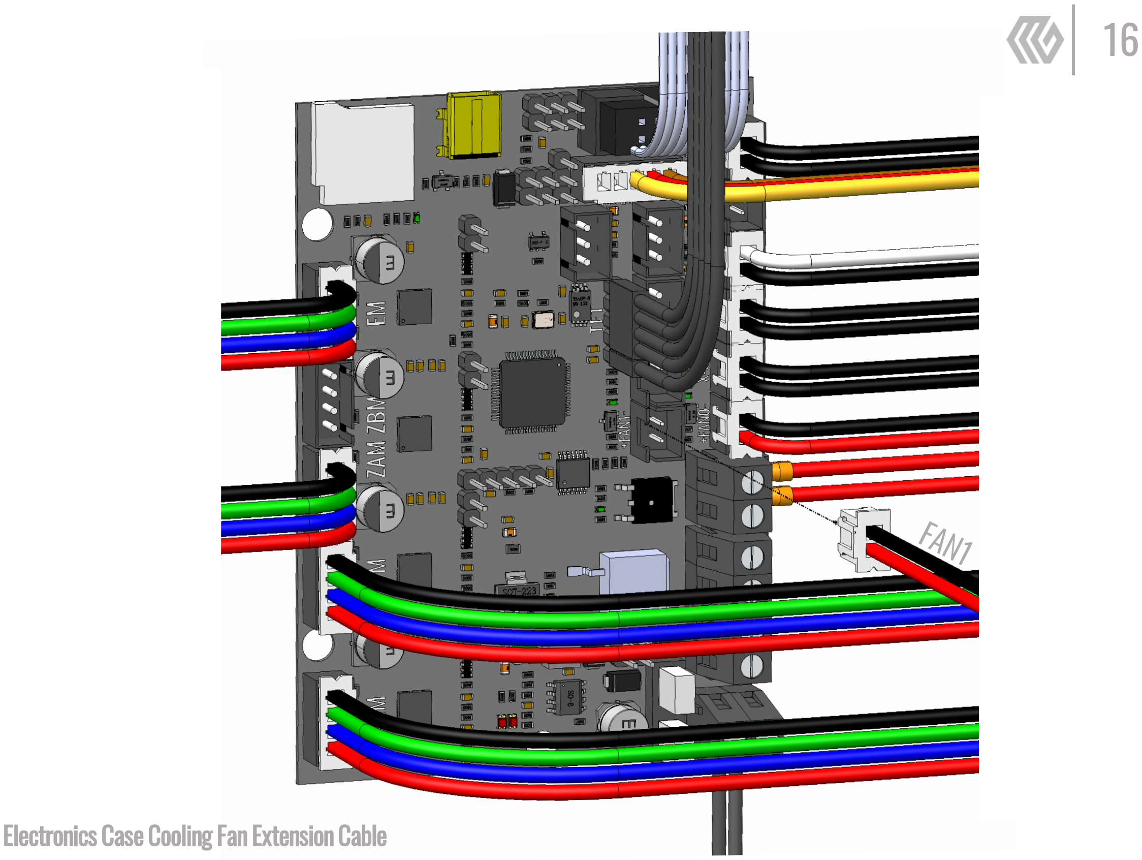
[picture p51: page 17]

## Electronics Case Cooling Fan Extension Cable

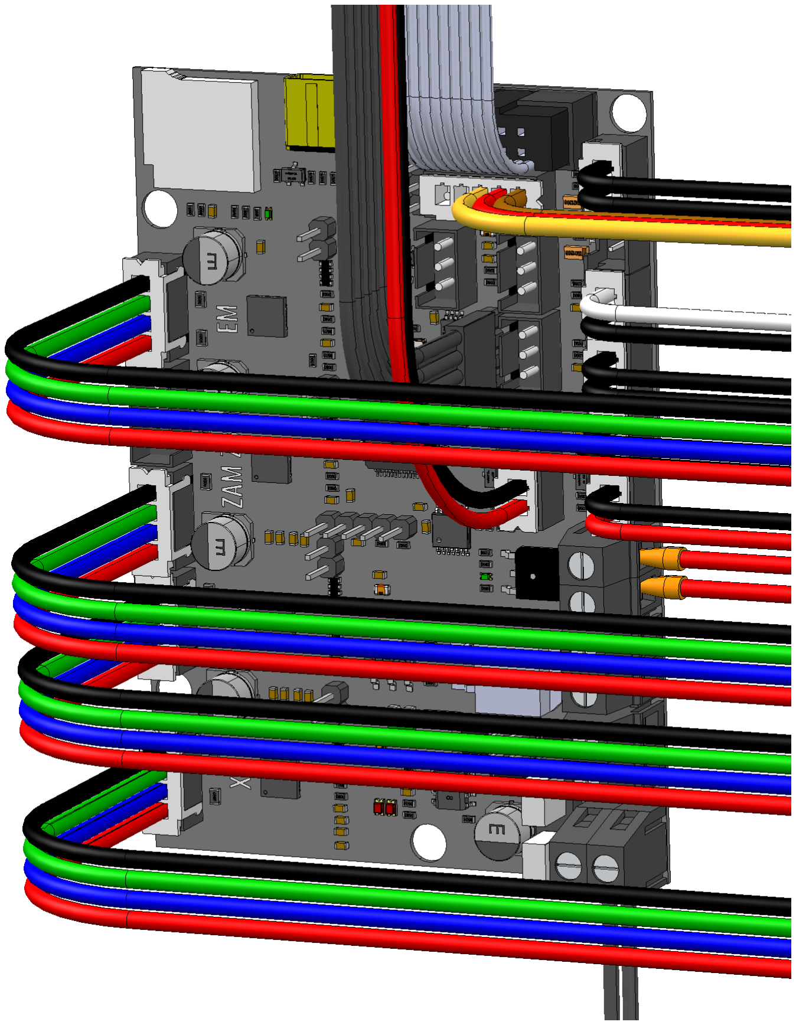
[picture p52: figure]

17

Well Done.

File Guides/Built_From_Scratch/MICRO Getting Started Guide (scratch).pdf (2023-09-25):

# MAKERGEAR

# MICRO

# GETTING STARTED GUIDE

## SCRATCH BUILT EDITION

# READ EVERYTHING PLEASE!

If you have chosen to build this thing from scratch, there are SO MANY little tiny things that might go wrong... So, we made one of our hyperactive engineers sit down & spend a COUNTLESS number of HOURS producing LOTS of detailed documentation to help YOU succeed. We’ll be honest there is like a LOT of verbiage in the next 10 pages & it might get boring, but you should read it. All of it. If not for yourself, do it for that poor engineer & the nights he worked late in

the hopes of making YOUR life easier.
Don’t let all that hard work be made in vain.


1

# BEFORE PLUGGING IN

# A Convenient Checklist to Make Sure Nothing Blows Up… Just Kidding

-Make sure you have properly uploaded the proper Marlin firmware provided on our GitHub onto a microSD card & that this card is inserted into the SKR board.
-The TFT28 Screen also requires its own firmware. Upload it onto a standard SD card & have it plugged into the screen before going further. -Check EVERY wire connection! Each connector used should provide a nice snug connection either popping into place or being latched together. NO connection should be loose or easily removable. If a connection does seem loose, double check that it is plugged into the correct location with the proper orientation.
-Check the pins on each individual wire. Make sure they are fully inserted into the JST connectors & that they are not broken or loose by giving them each a gentle tug.
-Physically slide the machine’s X, Y, & Z axis to confirm a proper mechanical assembly.
-Start with the Y axis by sliding the bed back & forth. Ensure that it travels smoothly without much resistance & can reach the Y End Stop successfully. The Y End Stop should click once the bed reaches it. When sliding the bed make sure the belt properly rotates both the Idler Pulley at the front of the machine, as well as the Drive Pulley mounted onto the Y Motor.
-Now check the X Axis by sliding the Hot End Mount from side to side. Confirm that it slides smoothly without interruption & that it successfully triggers the X End Stop once slid all the way to the left. Give the Hot End assembly a very light wiggle to check that it is securely fastened to the Hot End Mount. Lastly check that the belt is held snug withing the Hot End Mount by giving it a few gently tugs. This belt MUST be secure for your machine to succeed.
-Lastly check the Z Axis by turning the Z Knob both clockwise and counterclockwise. The entire X Axis assembly should move up & down relatively easy. You will feel the motor subtly click repeatedly as you manually rotate the Z Knob, this is normal. Make sure to not dig the tip of the nozzle into the bed when lowering or grind the entire assembly into the roof when raising the axis.
-Make sure to raise the Hot End at least an inch above the bed before plugging in your machine. The BL Touch Probe will deploy every time the machine is turned on and needs space to fully deploy or else it will fail its initial start up tests & the machine will need restarted.

2

# NOW PLUG IN!

# We are ALMOST there… Just a Little Housekeeping First

-As mentioned on the last page, once plugged in the BL Touch probe will initiate a short test in which it deploys & retracts twice each. If it does not do this, something could be wrong with the probe or its connection.
-Once the screen turns on & the firmware has finished installing, you might be greeted by the prompt below, in which case you’ll select “Touch Mode”

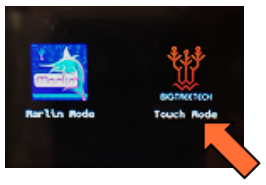
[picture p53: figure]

-Does “Marlin Mode” work with this device? Yes. Is it nearly as cool? NO… but if you insist or if you accidentally hit the wrong mode, pressing the screen’s knob like a button, and holding it for several seconds will allow you to return to this selection screen.
-You should end up at a screen like the one pictured below. You will also be greeted by a “Bed Leveling Failed” prompt. Ignore it. We’ll address that a few steps from now. Make sure to follow along with the orange arrows provided by this guide.

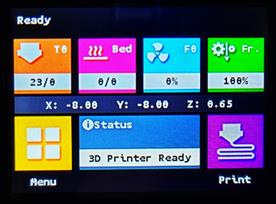
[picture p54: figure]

3

# AFTER PLUGGING IN

# These Next Steps MUST be Completed Before Your MICRO’s First Print

Next, we want to test the 3 axis motors by homing all 3 axis. Both the X and Y axis will move into their respective limit switches, activating them twice before settling into their home position. The Z axis will raise slightly & then lower the probe into the center of the bed twice. If all 3 of the axis home as described, proceed to the next step. If not, there could be an issue with your motor connections.

# HOW TO HOME YOUR MACHINE


Homing any 3D printer is like telling the machine where to start, and it lets the machine know where its Hot End is. From the “Home” screen, you can home any individual axis or all 3 at once by hitting the yellow “Home” button. Always make sure the bed is clear & nothing can impede the machine’s movement before homing. Let the homing sequence finish completely before advancing to the next steps.


4

# AFTER PLUGGING IN [cont.]

Once homing is completed, the probe offset must be set. This tells the MICRO how far the tip of the nozzle is from the tip of the BL Touch probe. If set correctly your first layers will be placed the perfect distance above the bed and will properly adhere to the bed surface. If this value is too high, the nozzle will be too far from the bed & none of the printed plastic will stick properly to the bed. If too low, the nozzle will be ground into the bed and the plastic will come out too squished or not at all.

# SETTING THE PROBE OFFSET

After “P Offset” is selected, the; From here you will need to grab the

machine will once again home the Z axis.


Place the Feeler Gauge beneath the tip of the nozzle and use the “Down” button to lower the nozzle towards the bed. Lower the nozzle until it just barely touches the Feeler Gauge. The increments in which the nozzle moves can be tweaked via the purple button initially labeled, “0.01mm”

Once you feel that the perfect offset value has been reached, hit the “Next” button twice or until the “Save” button appears next to hit. Select “Save” and the following prompt will pop up to which you respond, “OK” blue strip of plastic called a “Feeler Gauge” from the provided tool kit.

5

This setting is essentially the equivalent of Automatic Bed Leveling which will make sure that your first layers are always flat & flush with your bed. If not set properly, the nozzle will vary in its distance from the bed while printing. This can cause portions of the print to not stick properly or not extrude at all which will almost always cause your print to fail

# ACTIVATING BED LEVEL COMPENSATION


Pressing “Start” will lead into the machine’s probing sequence during which the printer will generate a mesh. This mesh basically let’s the printer know how the bed is shaped/slanted & will use the Z Motor to compensate for these variations while printing.


Return once more to the “Auto Bed Leveling” screen (found under the “Movement” option in the main menu)


Before returning to the main menu, make sure the BL Touch is activated by hitting this button. It should display “BL: on” and can be toggled on & off with each press.

# AFTER PLUGGING IN [cont.]

6

Finally, we will be loading filament into your MICRO. Only use a PLA that has a recommended printing temperature range that includes 190°C or below. You may need to straighten out the first couple inches of the filament’s end to help thread it into the filament drive.

# LOADING THE FILAMENT

# AFTER PLUGGING IN [cont.]


Increase the nozzle temperature to 190°C before returning to the “Movement” menu via the “Back” button. The left temperature value in white is the actual temp, while the right value is the temp you set it to.
You can adjust your temperature increments via the purple button initially labeled “5°C”


Pinch the lever of the MICRO’s filament drive to compress the spring. This will separate the brass drive gear from the silver bearing/pulley creating a space for you to feed an end of the filament up into the PTFE guide tube. Manually feed the filament until it reaches the hot end, and then use the screen to drive the filament further via the “Load” button. Continue to load filament until it extrudes out of the hot end’s nozzle in a smooth & uniform manner.

7

# STARTING YOUR FIRST PRINT

# Wow… Here We Go!

-Make sure one more time that the print bed is clear and free of debris.
-Confirm that your filament is loaded, and that the spool is placed within a spool holder directly next to the filament drive. This spool of filament must be fed directly upwards into the filament drive allowing the filament to unwind in a natural manner. -Plug the included SD Card into the SD slot next to the touch screen. This is where you’ll store gcodes for all of your prints. -Confirm your MICRO is placed on a sturdy surface in a well-ventilated space.
-Start your print…


-Once heated up, the machine will go directly into its first layers. Be prepared to cancel the print if the first layers are not adhering properly. If the nozzle simply seems slightly too close or too far, you can use the Z Knob to make small adjustments, one click at a time.

Select the gcode file you’d like to print. We suggest starting with the “MICROVase” as a test.

8

# PRINTING WITH THE MICRO

# A Random List of Tips & Tricks to Set You up for Success

-ONLY use PLA when printing. You made a 3D printed 3D printer NOT an industrial machine for prototyping with exotic materials.
-We suggest printing on this machine with a layer height of .2mm or higher.
-A print speed of 40mm per second or slower is highly recommended. This will decrease the likelihood of the belts slipping or the smaller X and Y motors from skipping. These problems can be recognized by layer shifts mid print.
-NEVER Exceed a printing temperature of 200°C. Since we are using such a small cooling fan, over time the heat might leak upwards & start melting your printer if the nozzle temp is set too high.
-For the same reason as the previous point, NEVER operate the printer if the Hot End’s cooling fan is malfunctioning. Make sure this fan is running at the start of EVERY print. The fan should come on automatically anytime the nozzle temperature exceeds 30°C
-DO NOT remove the PTFE tubing or Nozzle from the Hot End Assemble unless absolutely necessary. With this style of Hot End, removing/replacing either one of these will highly increase your chances of the assembly clogging or getting jammed.
-NEVER operate your printer without the included blue collar fit snug onto the Hot End Assembly. This ensures the PTFE tube stays in place & reduces the risk of filament clogs
-Unload the filament when your machine is not in use. Leaving filament loaded in the printer when it is not in use increases the likelihood of your printer’s nozzle getting clogged.
-Unplug the MICRO when it is not printing for extended periods of time. You MUST let the nozzle completely cool below 30°C before turning the unit off.
-Have fun creating new things with a machine YOU created!

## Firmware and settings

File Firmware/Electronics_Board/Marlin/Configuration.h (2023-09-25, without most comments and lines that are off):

#pragma once
#define CONFIGURATION_H_VERSION 02000901
#define STRING_CONFIG_H_AUTHOR "(none, default config)" // Who made the changes.
#define SHOW_BOOTSCREEN
#define SERIAL_PORT  2
#define BAUDRATE 115200
  #define MOTHERBOARD BOARD_BTT_SKR_MINI_E3_V2_0
#if LINEAR_AXES >= 4
  #define AXIS4_NAME 'A' // :['A', 'B', 'C', 'U', 'V', 'W']
#endif
#if LINEAR_AXES >= 5
  #define AXIS5_NAME 'B' // :['A', 'B', 'C', 'U', 'V', 'W']
#endif
#if LINEAR_AXES >= 6
  #define AXIS6_NAME 'C' // :['A', 'B', 'C', 'U', 'V', 'W']
#endif
#define EXTRUDERS 1
#define DEFAULT_NOMINAL_FILAMENT_DIA 1.75
#define TEMP_SENSOR_0 1
#define TEMP_SENSOR_1 0
#define TEMP_SENSOR_2 0
#define TEMP_SENSOR_3 0
#define TEMP_SENSOR_4 0
#define TEMP_SENSOR_5 0
#define TEMP_SENSOR_6 0
#define TEMP_SENSOR_7 0
#define TEMP_SENSOR_BED 0
#define TEMP_SENSOR_PROBE 0
#define TEMP_SENSOR_CHAMBER 0
#define TEMP_SENSOR_COOLER 0
#define TEMP_SENSOR_REDUNDANT 0
#define DUMMY_THERMISTOR_998_VALUE  25
#define DUMMY_THERMISTOR_999_VALUE 100
#define TEMP_RESIDENCY_TIME         2  // (seconds) Time to wait for hotend to "settle" in M109
#define TEMP_WINDOW                  4  // (°C) Temperature proximity for the "temperature reached" timer
#define TEMP_HYSTERESIS              3  // (°C) Temperature proximity considered "close enough" to the target
#define TEMP_BED_RESIDENCY_TIME     10  // (seconds) Time to wait for bed to "settle" in M190
#define TEMP_BED_WINDOW              1  // (°C) Temperature proximity for the "temperature reached" timer
#define TEMP_BED_HYSTERESIS          3  // (°C) Temperature proximity considered "close enough" to the target
#define TEMP_CHAMBER_RESIDENCY_TIME 10  // (seconds) Time to wait for chamber to "settle" in M191
#define TEMP_CHAMBER_WINDOW          1  // (°C) Temperature proximity for the "temperature reached" timer
#define TEMP_CHAMBER_HYSTERESIS      3  // (°C) Temperature proximity considered "close enough" to the target
#if TEMP_SENSOR_REDUNDANT
  #define TEMP_SENSOR_REDUNDANT_SOURCE     1  // The sensor that will provide the redundant reading.
  #define TEMP_SENSOR_REDUNDANT_TARGET     0  // The sensor that we are providing a redundant reading for.
  #define TEMP_SENSOR_REDUNDANT_MAX_DIFF  10  // (°C) Temperature difference that will trigger a print abort.
#endif
#define HEATER_0_MINTEMP   5
#define HEATER_1_MINTEMP   5
#define HEATER_2_MINTEMP   5
#define HEATER_3_MINTEMP   5
#define HEATER_4_MINTEMP   5
#define HEATER_5_MINTEMP   5
#define HEATER_6_MINTEMP   5
#define HEATER_7_MINTEMP   5
#define BED_MINTEMP        5
#define CHAMBER_MINTEMP    5
#define HEATER_0_MAXTEMP 275
#define HEATER_1_MAXTEMP 275
#define HEATER_2_MAXTEMP 275
#define HEATER_3_MAXTEMP 275
#define HEATER_4_MAXTEMP 275
#define HEATER_5_MAXTEMP 275
#define HEATER_6_MAXTEMP 275
#define HEATER_7_MAXTEMP 275
#define BED_MAXTEMP      150
#define CHAMBER_MAXTEMP  60
#define HOTEND_OVERSHOOT 15   // (°C) Forbid temperatures over MAXTEMP - OVERSHOOT
#define BED_OVERSHOOT    10   // (°C) Forbid temperatures over MAXTEMP - OVERSHOOT
#define COOLER_OVERSHOOT  2   // (°C) Forbid temperatures closer than OVERSHOOT
#define PIDTEMP
#define BANG_MAX 255     // Limits current to nozzle while in bang-bang mode; 255=full current
#define PID_MAX BANG_MAX // Limits current to nozzle while PID is active (see PID_FUNCTIONAL_RANGE below); 255=full current
#define PID_K1 0.95      // Smoothing factor within any PID loop
    #define DEFAULT_Kp  16.83
    #define DEFAULT_Ki   1.1
    #define DEFAULT_Kd  64.51
#define MAX_BED_POWER 255 // limits duty cycle to bed; 255=full current
#define MAX_CHAMBER_POWER 255 // limits duty cycle to chamber heater; 255=full current
  #define PID_FUNCTIONAL_RANGE 10 // If the temperature difference between the target temperature and the actual temperature
#define PREVENT_COLD_EXTRUSION
#define EXTRUDE_MINTEMP 170
#define PREVENT_LENGTHY_EXTRUDE
#define EXTRUDE_MAXLENGTH 200
#define THERMAL_PROTECTION_HOTENDS // Enable thermal protection for all extruders
#define THERMAL_PROTECTION_BED     // Enable thermal protection for the heated bed
#define THERMAL_PROTECTION_CHAMBER // Enable thermal protection for the heated chamber
#define THERMAL_PROTECTION_COOLER  // Enable thermal protection for the laser cooling
#define USE_XMIN_PLUG
#define USE_YMIN_PLUG
#define USE_ZMIN_PLUG
#define ENDSTOPPULLUPS
#define X_MIN_ENDSTOP_INVERTING false // Set to true to invert the logic of the endstop.
#define Y_MIN_ENDSTOP_INVERTING false // Set to true to invert the logic of the endstop.
#define Z_MIN_ENDSTOP_INVERTING false // Set to true to invert the logic of the endstop.
#define I_MIN_ENDSTOP_INVERTING false // Set to true to invert the logic of the endstop.
#define J_MIN_ENDSTOP_INVERTING false // Set to true to invert the logic of the endstop.
#define K_MIN_ENDSTOP_INVERTING false // Set to true to invert the logic of the endstop.
#define X_MAX_ENDSTOP_INVERTING false // Set to true to invert the logic of the endstop.
#define Y_MAX_ENDSTOP_INVERTING false // Set to true to invert the logic of the endstop.
#define Z_MAX_ENDSTOP_INVERTING false // Set to true to invert the logic of the endstop.
#define I_MAX_ENDSTOP_INVERTING false // Set to true to invert the logic of the endstop.
#define J_MAX_ENDSTOP_INVERTING false // Set to true to invert the logic of the endstop.
#define K_MAX_ENDSTOP_INVERTING false // Set to true to invert the logic of the endstop.
#define Z_MIN_PROBE_ENDSTOP_INVERTING false // Set to true to invert the logic of the probe.
#define X_DRIVER_TYPE  TMC2209
#define Y_DRIVER_TYPE  TMC2209
#define Z_DRIVER_TYPE  TMC2209
#define E0_DRIVER_TYPE TMC2209
#define DEFAULT_AXIS_STEPS_PER_UNIT   { 80, 80, 400, 94.3 }
#define DEFAULT_MAX_FEEDRATE          { 300, 300, 20, 30 }
#define DEFAULT_MAX_ACCELERATION      { 450, 450, 10, 2000 }
#define DEFAULT_ACCELERATION          450    // X, Y, Z and E acceleration for printing moves
#define DEFAULT_RETRACT_ACCELERATION  2000    // E acceleration for retracts
#define DEFAULT_TRAVEL_ACCELERATION   450    // X, Y, Z acceleration for travel (non printing) moves
#define DEFAULT_EJERK    10  // May be used by Linear Advance
  #define JUNCTION_DEVIATION_MM 0.013 // (mm) Distance from real junction edge
  #define JD_HANDLE_SMALL_SEGMENTS    // Use curvature estimation instead of just the junction angle
#define Z_MIN_PROBE_USES_Z_MIN_ENDSTOP_PIN
#define USE_PROBE_FOR_Z_HOMING
#define BLTOUCH
#define NOZZLE_TO_PROBE_OFFSET { -2, 40, -1 }
#define PROBING_MARGIN 10
#define XY_PROBE_FEEDRATE (133*60)
#define Z_PROBE_FEEDRATE_FAST (4*60)
#define Z_PROBE_FEEDRATE_SLOW (Z_PROBE_FEEDRATE_FAST / 2)
#define MULTIPLE_PROBING 2
#define Z_CLEARANCE_DEPLOY_PROBE   10 // Z Clearance for Deploy/Stow
#define Z_CLEARANCE_BETWEEN_PROBES  5 // Z Clearance between probe points
#define Z_CLEARANCE_MULTI_PROBE     5 // Z Clearance between multiple probes
#define Z_PROBE_LOW_POINT          -2 // Farthest distance below the trigger-point to go before stopping
#define Z_PROBE_OFFSET_RANGE_MIN -20
#define Z_PROBE_OFFSET_RANGE_MAX 20
#define X_ENABLE_ON 0
#define Y_ENABLE_ON 0
#define Z_ENABLE_ON 0
#define E_ENABLE_ON 0 // For all extruders
#define DISABLE_X false
#define DISABLE_Y false
#define DISABLE_Z false
#define DISABLE_E false             // Disable the extruder when not stepping
#define DISABLE_INACTIVE_EXTRUDER   // Keep only the active extruder enabled
#define INVERT_X_DIR false
#define INVERT_Y_DIR false
#define INVERT_Z_DIR false
#define INVERT_E0_DIR true
#define INVERT_E1_DIR false
#define INVERT_E2_DIR false
#define INVERT_E3_DIR false
#define INVERT_E4_DIR false
#define INVERT_E5_DIR false
#define INVERT_E6_DIR false
#define INVERT_E7_DIR false
#define X_HOME_DIR -1
#define Y_HOME_DIR -1
#define Z_HOME_DIR -1
#define X_BED_SIZE 89
#define Y_BED_SIZE 89
#define X_MIN_POS -8
#define Y_MIN_POS -8
#define Z_MIN_POS 0
#define X_MAX_POS 81
#define Y_MAX_POS 81
#define Z_MAX_POS 100
#define MIN_SOFTWARE_ENDSTOPS
  #define MIN_SOFTWARE_ENDSTOP_X
  #define MIN_SOFTWARE_ENDSTOP_Y
  #define MIN_SOFTWARE_ENDSTOP_Z
  #define MIN_SOFTWARE_ENDSTOP_I
  #define MIN_SOFTWARE_ENDSTOP_J
  #define MIN_SOFTWARE_ENDSTOP_K
#define MAX_SOFTWARE_ENDSTOPS
  #define MAX_SOFTWARE_ENDSTOP_X
  #define MAX_SOFTWARE_ENDSTOP_Y
  #define MAX_SOFTWARE_ENDSTOP_Z
  #define MAX_SOFTWARE_ENDSTOP_I
  #define MAX_SOFTWARE_ENDSTOP_J
  #define MAX_SOFTWARE_ENDSTOP_K
#define AUTO_BED_LEVELING_BILINEAR
#define DEBUG_LEVELING_FEATURE
  #define ENABLE_LEVELING_FADE_HEIGHT
    #define DEFAULT_LEVELING_FADE_HEIGHT 10.0 // (mm) Default fade height.
  #define SEGMENT_LEVELED_MOVES
  #define LEVELED_SEGMENT_LENGTH 5.0 // (mm) Length of all segments (except the last one)
  #define G26_MESH_VALIDATION
    #define MESH_TEST_NOZZLE_SIZE    0.4  // (mm) Diameter of primary nozzle.
    #define MESH_TEST_LAYER_HEIGHT   0.2  // (mm) Default layer height for G26.
    #define MESH_TEST_HOTEND_TEMP  200    // (°C) Default nozzle temperature for G26.
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

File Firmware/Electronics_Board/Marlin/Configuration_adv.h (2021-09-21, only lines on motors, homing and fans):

  #define CONTROLLER_FAN_PIN PC7        // Set a custom pin for the controller fan
#define E0_AUTO_FAN_PIN PC6
#define E1_AUTO_FAN_PIN -1
#define E2_AUTO_FAN_PIN -1
#define E3_AUTO_FAN_PIN -1
#define E4_AUTO_FAN_PIN -1
#define E5_AUTO_FAN_PIN -1
#define E6_AUTO_FAN_PIN -1
#define E7_AUTO_FAN_PIN -1
#define CHAMBER_AUTO_FAN_PIN -1
#define COOLER_AUTO_FAN_PIN -1
#define COOLER_FAN_PIN -1
#define HOMING_BUMP_MM      { 5, 5, 2 }       // (mm) Backoff from endstops after first bump
#define HOMING_BUMP_DIVISOR { 2, 2, 4 }       // Re-Bump Speed Divisor (Divides the Homing Feedrate)
#define MICROSTEP_MODES { 16, 16, 16, 16, 16, 16 } // [1,2,4,8,16]
    #define X_CURRENT       200        // (mA) RMS current. Multiply by 1.414 for peak current.
    #define X_CURRENT_HOME  X_CURRENT  // (mA) RMS current for sensorless homing
    #define X_MICROSTEPS     16        // 0..256
    #define Y_CURRENT       200
    #define Y_CURRENT_HOME  Y_CURRENT
    #define Y_MICROSTEPS     16
    #define Z_CURRENT       800
    #define Z_CURRENT_HOME  Z_CURRENT
    #define Z_MICROSTEPS     16
    #define E0_CURRENT      800
    #define E0_MICROSTEPS    16
  #define X_HYBRID_THRESHOLD     100  // [mm/s]
  #define X2_HYBRID_THRESHOLD    100
  #define Y_HYBRID_THRESHOLD     100
  #define Y2_HYBRID_THRESHOLD    100
  #define Z_HYBRID_THRESHOLD       3
  #define Z2_HYBRID_THRESHOLD      3
  #define Z3_HYBRID_THRESHOLD      3
  #define Z4_HYBRID_THRESHOLD      3
  #define I_HYBRID_THRESHOLD       3
  #define J_HYBRID_THRESHOLD       3
  #define K_HYBRID_THRESHOLD       3
  #define E0_HYBRID_THRESHOLD     30
  #define E1_HYBRID_THRESHOLD     30
  #define E2_HYBRID_THRESHOLD     30
  #define E3_HYBRID_THRESHOLD     30
  #define E4_HYBRID_THRESHOLD     30
  #define E5_HYBRID_THRESHOLD     30
  #define E6_HYBRID_THRESHOLD     30
  #define E7_HYBRID_THRESHOLD     30

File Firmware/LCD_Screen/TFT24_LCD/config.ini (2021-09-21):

#--------------------------------------------------------------------
#
# DEFAULT CONFIG FILE FOR BigTreeTech TFT CONTROLLERS
#
#--------------------------------------------------------------------


#--------------------------------------------------------------------
# Supported TFT Variants
#--------------------------------------------------------------------
#
# BIGTREE_TFT35_V1_0    / BIGTREE_TFT35_V1_1 / BIGTREE_TFT35_V1_2
# BIGTREE_TFT35_V2_0    / BIGTREE_TFT35_V3_0 / BIGTREE_TFT35_E3_V3_0
# BIGTREE_TFT35_B1_V3_0 / BIGTREE_TFT43_V3_0 / BIGTREE_TFT50_V3_0
# BIGTREE_TFT70_V3_0    / BIGTREE_TFT28_V1_0 / BIGTREE_TFT28_V3_0
# BIGTREE_TFT24_V1_1    / MKS_TFT32_V1_3     / MKS_TFT32_V1_4
# MKS_TFT28_V3_0        / MKS_TFT28_V4_0
#
# Firmware source: https://github.com/bigtreetech/BIGTREETECH-TouchScreenFirmware


#--------------------------------------------------------------------
# Supported Marlin Firmware Versions
#--------------------------------------------------------------------
#
# Minimum Marlin firmware version: 2.0.5.4
# Distribution date: 2020-05-12
# Firmware source: https://github.com/MarlinFirmware/Marlin/releases
#
# In order the TFT firmware is able to provide all of its functionalities/features,
# ensure that the following options are enabled in Marlin firmware.
#
# General options:
#   EEPROM_SETTINGS (in Configuration.h)
#   AUTO_REPORT_TEMPERATURES (in Configuration_adv.h)
#   M115_GEOMETRY_REPORT (in Configuration_adv.h)
#   M114_DETAIL (in Configuration_adv.h)
#   REPORT_FAN_CHANGE (in Configuration_adv.h)
#
# Options to support printing from onboard SD:
#   SDSUPPORT (in Configuration.h)
#   LONG_FILENAME_HOST_SUPPORT (in Configuration_adv.h)
#   AUTO_REPORT_SD_STATUS (in Configuration_adv.h)
#   SDCARD_CONNECTION ONBOARD (in Configuration_adv.h)
#
# Options to support dialog with host:
#   EMERGENCY_PARSER (in Configuration_adv.h)
#   SERIAL_FLOAT_PRECISION 4 (in Configuration_adv.h)
#   HOST_ACTION_COMMANDS (in Configuration_adv.h)
#   HOST_PROMPT_SUPPORT (in Configuration_adv.h)
#
# Options to support M600 with host & (Un)Load menu:
#   Options to support dialog with host (as pre requisite)
#   NOZZLE_PARK_FEATURE (in Configuration.h)
#   ADVANCED_PAUSE_FEATURE (in Configuration_adv.h)
#   PARK_HEAD_ON_PAUSE (in Configuration_adv.h)
#   FILAMENT_LOAD_UNLOAD_GCODES (in Configuration_adv.h)
#
# Options to support Babystep menu:
#   BABYSTEPPING (in Configuration_adv.h)
#
# Options to support repeatibility test to test probe accuracy (M48):
#   Z_MIN_PROBE_REPEATABILITY_TEST (in Configuration.h)
#
# Options to support aligment of multiple Z steppers using a bed probe (G34):
#   Z_STEPPER_AUTO_ALIGN (in Configuration_adv.h)

#--------------------------------------------------------------------
# General Settings
#--------------------------------------------------------------------

#### Enable Status Screen
# Status screen or home screen displays the current temperature, fan and speeds.
# If this disabled, the main menu will become the default home screen.
#   Options: [Enable: 1, Disable: 0]
status_screen:1

#### Baudrate / Connection speed
# This baudrate setting is used for serial connection to the printer and other serial hosts like ESP8266.
#   Options: [2400: 0, 9600: 1, 19200: 2, 38400: 3, 57600: 4, 115200: 5, 250000: 6, 500000: 7, 1000000: 8]
baudrate:5

#### Default Touch Mode Language
# Select the language to display on the LCD while in Touch Mode.
# To add/flash a second language copy the required "language_xx.ini" file from "Language Packs" folder
# to the SD root folder. Then preset the reset button to load/flash the copied language file.
#   Options: [primary language (english): 0, secondary language: 1]
language:0

#### Default Touch Mode Colors
# Set colors used in touchscreen mode.
# Select an option from the provide list or set the color (RGB888 format) hex value directly (start with “0x”),
# such as: Red: 0xFF0000, Green: 0x00FF00, Blue: 0x0000FF.
#   Options: [ WHITE: 0,  BLACK: 1,  RED: 2,  GREEN: 3,      BLUE: 4,       CYAN: 5,  MAGENTA: 6,    YELLOW: 7,
#             ORANGE: 8, PURPLE: 9, LIME: 10, BROWN: 11, DARKBLUE: 12, DARKGREEN: 13,    GRAY: 14, DARKGRAY: 15]

## Title background color
title_back_color:1

## Background color
background_color:1

## Font foreground color
font_color:0

## Reminder font color, such as: "No print attached", "Busy processing", etc
reminder_color:2

## Volume status/reminder font color, such as: "Card inserted", "Card removed"
volume_status_color:5

## Backgroud color for X Y Z position display in Status Screen menu
status_xyz_bg_color:15

## List View border color
list_border_color:15

## List View button background color
list_button_bg_color:15

## Color used by the Mesh Editor menu for drawing the mesh with the minimun value in the grid
mesh_min_color:7

## Color used by the Mesh Editor menu for drawing the mesh with the maximum value in the grid
mesh_max_color:2
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

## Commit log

2021-09-10 Uploaded V1.0
    [Configuration.h, Configuration_adv.h, MicroBeta_Base.STL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]
2021-09-10 Uploaded Assembly Guide
2021-09-21 v1.0.1
    * Updated file structure
    * Tweaked acceleration settings
    * Fixed STL/STEP file semantics
    * Added the Simplify3D printer profile
    * General improvements to the README page
    [Configuration.h, Configuration_adv.h, MicroBeta_Base.STL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]
2021-11-05 v1.0.2
    * Updated the assembly guide
    * Updated the STL/STEP file names
    * Tweaked STL/STEP file hole sizes
    * Added elephant feet to the corners of the 'base' and 'top' printed parts
    [Bed.STEP, Bed.stl, BedClip.STEP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]
2023-09-25 Update base branch (#1)
    * Update README.md
    * Update README.md
    Updated the Micro photo
    * Update README.md
    * Update README.md
    * Update README.md
    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
    [Bed.STEP, Bed.stl, BedClip.STEP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]

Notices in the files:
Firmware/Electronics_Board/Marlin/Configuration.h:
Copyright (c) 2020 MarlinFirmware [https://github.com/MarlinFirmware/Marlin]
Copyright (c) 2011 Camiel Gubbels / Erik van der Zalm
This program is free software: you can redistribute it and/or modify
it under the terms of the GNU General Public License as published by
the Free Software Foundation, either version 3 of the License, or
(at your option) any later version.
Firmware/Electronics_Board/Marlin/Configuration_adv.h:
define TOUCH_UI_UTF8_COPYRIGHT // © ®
